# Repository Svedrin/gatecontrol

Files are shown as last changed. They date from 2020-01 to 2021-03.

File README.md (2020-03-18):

# GateControl

ESP8266 firmware that implements a garage gate controller.

# Physical setup

You'll need:

* a garage gate equipped with a motor
* one sensor each at the top and bottom end positions to locate the gate
* a light barrier
* WiFi, MQTT
* a signal light with which you warn people before automatically closing the gate.

# NodeRED

For GUI and for controlling the signal light, I use NodeRED. Here's the flow:

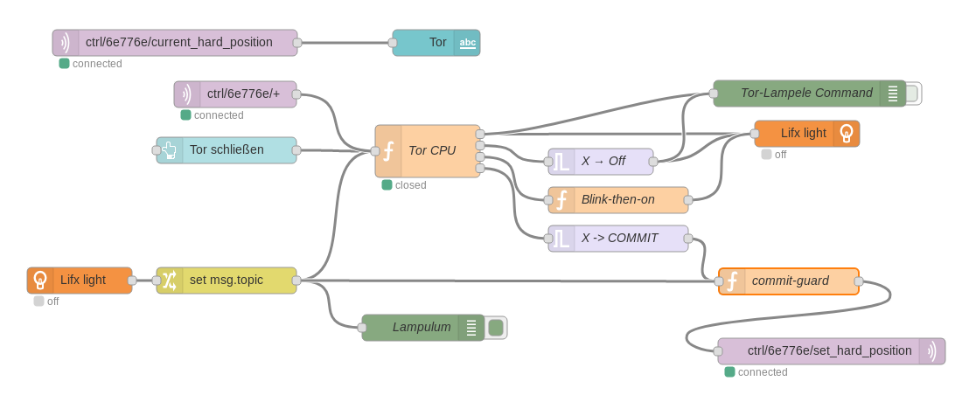
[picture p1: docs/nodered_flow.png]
nodered_flow


The main part of the setup is [the CPU node](nodered/cpu.js). Its state machine can be admired here:

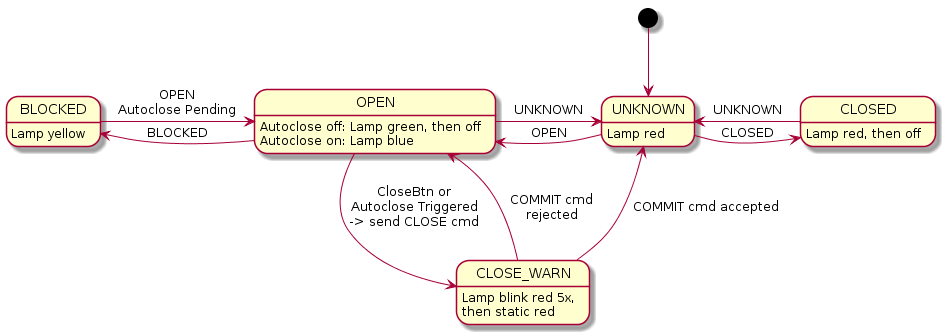
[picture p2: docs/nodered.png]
nodered


# Status indication

The controller regularly publishes the current state of the gate on the `ctrl/<ChipID>/current_hard_position` MQTT topic. You can (and should) use this information to drive a signal light, or monitor for the `ERROR` state.

I'm using a LIFX light bulb for the signal light:

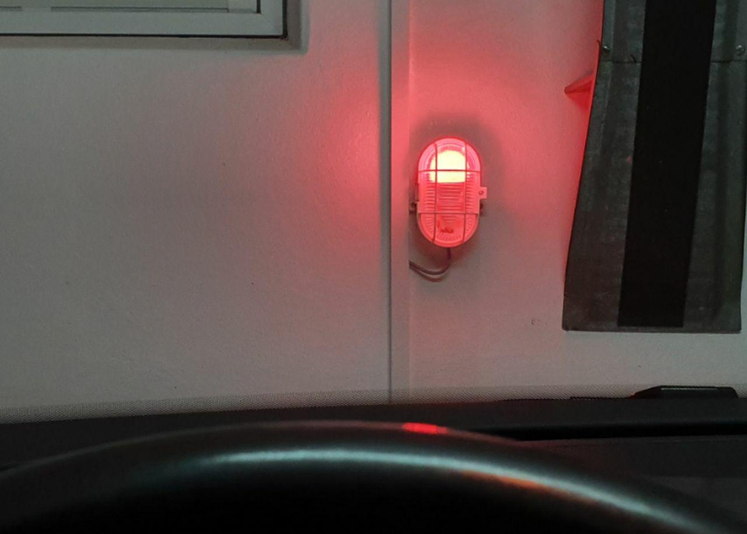
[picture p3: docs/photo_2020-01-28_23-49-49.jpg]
signal


# Controller State Machine

The controller's state machine is focused on providing all the features in a safe way. That means, whatever weird situation we're faced with, the objective is to never make it _worse_. This is achieved by inserting yield points into the state machine, where external commands are necessary to continue. If such a command arrives, we can safely assume that warnings are taken care of. Otherwise, we cannot know what's going on, so we have to abort and return to a safe state.

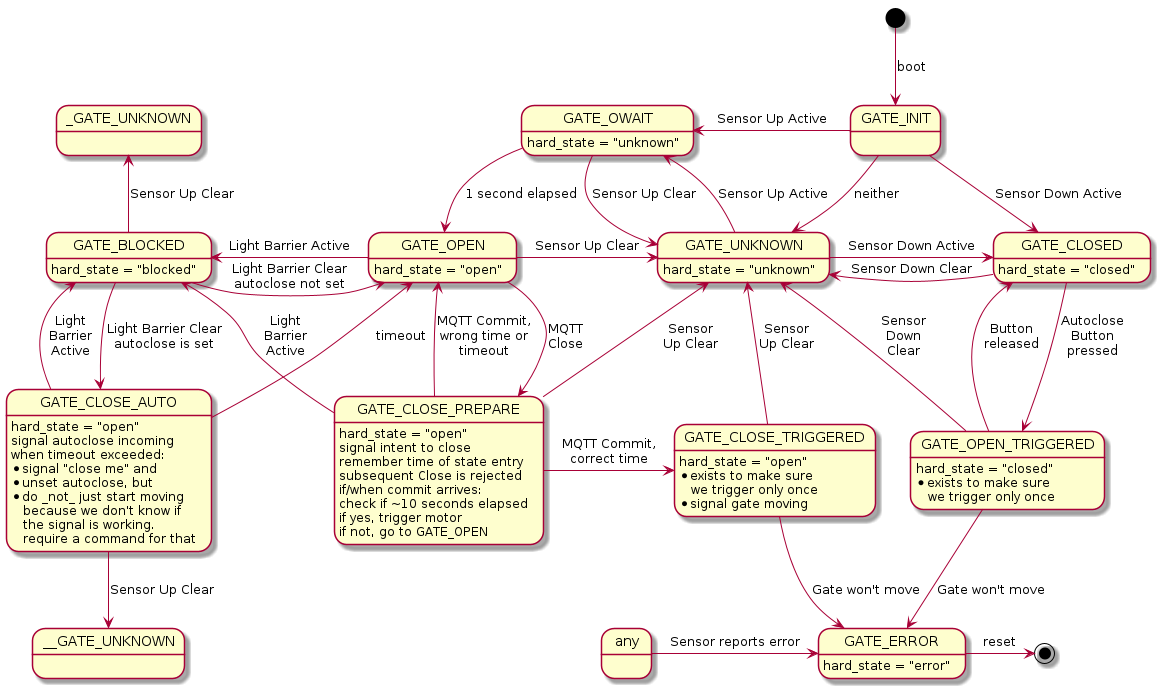
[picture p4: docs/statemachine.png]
statemachine


# Autoclosing

When you want to leave the garage, having to close the gate manually can be a nuisance. Thus the controller supports autoclose, through a separate physical button connected to one of the inputs. The controller then monitors the light barrier, and if it was clear for a while, automatically closes the gate. Again, using the status indications published on `ctrl/<ChipID>/autoclose` to drive a signal light is highly encouraged.

# Remote closing

To command the controller to close the gate:

* send an MQTT message of `CLOSED` to `ctrl/<ChipID>/set_hard_position`.
* If the controller accepted the command, it acknowledges by sending `waiting` to the `ctrl/<ChipID>/close_ack` topic.
* You should now trigger the signal light to show a warning that indicates clearly that the gate is about to move.
* 10 seconds (± some wiggle room) after you sent the initial `CLOSED` command, send `COMMIT` to `ctrl/<ChipID>/set_hard_position`.
* If the controller is satisfied with your timing, it replies with `commit` on `ctrl/<ChipID>/close_ack`.
* The controller triggers the gate to start moving and sends `closing` on `ctrl/<ChipID>/close_ack`.

This scheme basically implements [two-phase commit](https://en.wikipedia.org/wiki/Two-phase_commit_protocol). It is meant to ensure that when individual components fail (like the signal light being unavailable or NodeRED being restarted), the gate does not start moving unexpectedly.

# ESP Pinout

Here's how things need to be connected to the ESP. Comments indicate glitches and caveats, most of which are to do with earlier versions of my PCB being less than ideal. I'll probably need to re-do mine so that I can fix these.

All inputs need to be pulled low when they are active, and high otherwise.

| Input | Pin | Output | Comment |
| --- | --- | --- | --- |
| Sensor Monitor | D0 | | not yet implemented |
| Sensor Up | D1 | | needs external pull-up |
| Sensor Down | D2 | | needs external pull-up |
| Autoclose button | D3 | | must not be pulled low during boot |
| | D4 | Error LED | ESP on-board LED, LOW = on |
| | D5 | Gate Trigger | HIGH = on |
| Lightbarrier blocked | D6 | | |
| Lightbarrier clear | D7 | | |
| | D8 | Status LED | HIGH = on |

Note that while it would probably be better to drive the Status LED and the trigger relay by pulling their pins LOW, we can't really do that since that would incur quirky boot behavior. We really do _not_ want the gate to start moving uncontrollably whenever the ESP is reset, and those pins are pulled LOW during boot, so LOW _must_ mean "off".

Also note that I'm thinking about re-using the Status LED to also drive a relay to enable the Light Barrier only when needed. In that case its behavior would change, because blinking would be a really bad idea (or I'd need to debounce that in the hardware, ugh).

# LEDs

* Error LED: Blinks while connecting to WiFi, off while running, static when error
* Status LED: Static when autoclose enabled, blinks when about to close

# Disclaimer

I broke my gate once during this project, and it's somewhat probable that so will you. I'm obviously not liable for any damages you cause using this project.

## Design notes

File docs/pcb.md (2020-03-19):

# PCB design

The PCB is designed using Fritzing. The breadboard part is not overly accurate and probably won't work (the relays don't fit).

# Relay: SONGLE SRD-05VDC-SL-C

The Fritzing part is from here:

https://github.com/bluewalk/Fritzing-Parts/tree/master/SRD-5VDC-SL-C

Amazon Link for the relays:

https://www.amazon.de/gp/product/B009APPHAE/ref=ppx_yo_dt_b_asin_title_o00_s00?ie=UTF8&psc=1

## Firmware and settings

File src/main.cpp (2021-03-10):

#pragma GCC diagnostic push  // save compiler settings
#pragma GCC diagnostic error "-Wall"

// kate: hl c++
#include <ESP8266WiFi.h>
#include <PubSubClient.h>

// this file #defines WIFI_SSID and WIFI_PASSWORD
#include <WifiParams.h>

#include <monitoredsensor.h>
#include <statemachine.h>

#define PIN_MON        D0 // Low while all sensors are working
#define PIN_UP         D1 // Low when the gate is up
#define PIN_DN         D2 // Low when the gate is down
#define PIN_AUTOCLOSE  D3 // Low when user presses the autoclose button
#define PIN_ERRORLED   D4 // Blinks while connecting, off while running, static when error
#define PIN_TRIGGER    D5 // Relay that triggers the gate
#define PIN_LB_BLOCKED D6 // Light barrier says "I'm blocked"
#define PIN_LB_CLEAR   D7 // Light barrier says "I'm clear"
#define PIN_STATUSLED  D8 // Static when autoclose enabled, blinks when about to close

WiFiClient espClient;
PubSubClient client(espClient);
StateMachine state_machine;
MonitoredSensor light_barrier(PIN_LB_BLOCKED, PIN_LB_CLEAR, LOW, true);

unsigned long last_tick;
unsigned long last_msg;
char hard_pos[50];
char prev_hard_pos[50];

char mqtt_topic_state[50];
char mqtt_topic_commands[50];
char mqtt_topic_command_acks[50];
char mqtt_topic_autoclose[50];

#define MQTT_TOPIC(which_one, topic_suffix) strncpy( \
        which_one, \
        ("ctrl/" + String(ESP.getChipId(), HEX) + "/" + topic_suffix).c_str(), \
        sizeof(which_one) \
    )

void on_mqtt_message(char* topic, byte* payload, unsigned int length);

void reconnect() {
    // Loop until we're reconnected
    while (!client.connected()) {
        Serial.print("Attempting MQTT connection...");
        // Attempt to connect
        String clientId = "ESP8266Client-" + String(ESP.getChipId(), HEX);
        if (client.connect(clientId.c_str(), MQTT_USERNAME, MQTT_PASSWORD)) {
            client.subscribe(mqtt_topic_commands);
            Serial.println("connected");
        } else {
            Serial.print("failed, rc=");
            Serial.print(client.state());
            Serial.println(" try again in 5 seconds");
            // Wait 5 seconds before retrying
            delay(5000);
        }
    }
}

void setup(void)
{
    // Configure pins
    pinMode(PIN_MON,        INPUT);
    pinMode(PIN_UP,         INPUT);
    pinMode(PIN_DN,         INPUT);
    pinMode(PIN_AUTOCLOSE,  INPUT_PULLUP);
    pinMode(PIN_LB_BLOCKED, INPUT_PULLUP);
    pinMode(PIN_LB_CLEAR,   INPUT_PULLUP);

    pinMode(PIN_ERRORLED,  OUTPUT);
    pinMode(PIN_STATUSLED, OUTPUT);
    pinMode(PIN_TRIGGER,   OUTPUT);

    digitalWrite(PIN_ERRORLED,  LOW);
    digitalWrite(PIN_STATUSLED, LOW);
    digitalWrite(PIN_TRIGGER,   LOW);

    // Start Serial
    Serial.begin(115200);

    // Populate topic names
    MQTT_TOPIC(mqtt_topic_state,        "current_hard_position");
    MQTT_TOPIC(mqtt_topic_commands,     "set_hard_position");
    MQTT_TOPIC(mqtt_topic_command_acks, "close_ack");
    MQTT_TOPIC(mqtt_topic_autoclose,    "autoclose");

    Serial.print("State topic: ");
    Serial.println(mqtt_topic_state);

    // Connect to WiFi
    int error_led_state = LOW;
    WiFi.begin(WIFI_SSID, WIFI_PASSWORD);
    WiFi.mode(WIFI_STA);
    Serial.println();
    while (WiFi.status() != WL_CONNECTED) {
        digitalWrite(PIN_ERRORLED, error_led_state);
        error_led_state = (error_led_state == HIGH ? LOW : HIGH);
        delay(500);
        Serial.print(".");
    }
    Serial.println("");
    Serial.println("WiFi connected");
    digitalWrite(PIN_ERRORLED,  HIGH);

    // Print the IP address
    Serial.println(WiFi.localIP());

    randomSeed(micros());

    client.setServer(MQTT_HOST, MQTT_PORT);
    client.setCallback(on_mqtt_message);

    last_tick = 0;
    last_msg  = 0;
}


void on_mqtt_message(char* topic, byte* payload, unsigned int length) {
    char buf[50];
    if( length > sizeof(buf) - 1 ){
        length = sizeof(buf) - 1;
    }
    memcpy(buf, payload, length);
    buf[length] = 0;

    Serial.print("Message arrived [");
    Serial.print(topic);
    Serial.print("] = ");
    Serial.print(buf);

    if( strcmp(topic, mqtt_topic_commands) == 0 ){
        if(strncmp((const char *)payload, "CLOSED", length) == 0){
            Serial.println("Received CLOSE message");
            if (state_machine.cmd_close(millis()) == COMMAND_ACCEPTED) {
                client.publish(mqtt_topic_command_acks, "waiting");
            } else {
                client.publish(mqtt_topic_command_acks, "reject");
            }
        }
        else if(strncmp((const char *)payload, "COMMIT", length) == 0){
            Serial.println("Received COMMIT message");
            if (state_machine.cmd_commit(millis()) == COMMAND_ACCEPTED) {
                client.publish(mqtt_topic_command_acks, "commit");
            } else {
                client.publish(mqtt_topic_command_acks, "abort");
            }
        }
    }
}

void loop() {
    if (!client.connected()) {
        reconnect();
    }

    client.loop();

    unsigned long now = millis();

    if(now > last_tick + 100){
        last_tick = now;

        esp_state_t esp_state;
        esp_state.sensor_gate_up   = (digitalRead(PIN_UP) == LOW ? SENSOR_ACTIVE : SENSOR_CLEAR);
        esp_state.sensor_gate_down = (digitalRead(PIN_DN) == LOW ? SENSOR_ACTIVE : SENSOR_CLEAR);
        esp_state.button_autoclose = (digitalRead(PIN_AUTOCLOSE) == LOW ? SENSOR_ACTIVE : SENSOR_CLEAR);
        esp_state.sensor_light_barrier = light_barrier.read(now);
        esp_state.millis = now;

        step_t step = state_machine.step(&esp_state);

        switch(step.current_state){
            case GATE_INIT:
                strcpy(hard_pos, "INIT");
                break;

            case GATE_OPEN:
            case GATE_CLOSE_AUTO:
            case GATE_CLOSE_PREPARE:
            case GATE_CLOSE_TRIGGERED:
                strcpy(hard_pos, "OPEN");
                break;

            case GATE_BLOCKED:
                strcpy(hard_pos, "BLOCKED");
                break;

            case GATE_OWAIT:
            case GATE_UNKNOWN:
                strcpy(hard_pos, "UNKNOWN");
                break;

            case GATE_CLOSED:
            case GATE_OPEN_TRIGGERED:
                strcpy(hard_pos, "CLOSED");
                break;

            case GATE_ERROR:
                strcpy(hard_pos, "ERROR");
                digitalWrite(PIN_ERRORLED, LOW);
                break;
        }

        if(now > last_msg + 1000 || strcmp(hard_pos, prev_hard_pos) != 0){
            last_msg = now;
            strcpy(prev_hard_pos, hard_pos);
            client.publish(mqtt_topic_state, hard_pos);

            Serial.print("Hard position = ");
            Serial.println(hard_pos);
        }

        // autoclose_state indicates when certain events have happened
        // and are only set for the one step where they happened
        if (step.autoclose_state == AUTOCLOSE_ENABLED) {
            client.publish(mqtt_topic_autoclose, "enabled");
        }
        else if (step.autoclose_state == AUTOCLOSE_PENDING) {
            client.publish(mqtt_topic_autoclose, "pending");
        }
        else if (step.autoclose_state == AUTOCLOSE_RESET) {
            client.publish(mqtt_topic_autoclose, "reset");
        }
        else if (step.autoclose_state == AUTOCLOSE_TRIGGERED) {
            client.publish(mqtt_topic_autoclose, "triggered");
        }

        // Drive the status LED.
        // When we received a CLOSE command, blink (by only lighting
        // up for the second half of each second)
        if (step.current_state == GATE_CLOSE_PREPARE) {
            digitalWrite(PIN_STATUSLED, (now % 1000 > 500 ? HIGH : LOW));
        }
        // When autoclose is enabled, light up statically
        else if (step.autoclose_state == AUTOCLOSE_ON) {
            digitalWrite(PIN_STATUSLED, HIGH);
        }
        // Otherwise, go dark
        else {
            digitalWrite(PIN_STATUSLED, LOW);
        }

        if (step.trigger) {
            Serial.println("trigger! pew pew");
            digitalWrite(PIN_TRIGGER, HIGH);
            delay(500);
            digitalWrite(PIN_TRIGGER, LOW);
        }
    }

    delay(1);
}

#pragma GCC diagnostic pop // Restore compiler settings

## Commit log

2020-01-22 refactor LOW and HIGH to SENSOR_ACTIVE and SENSOR_CLEAR
2020-01-22 install wheel support for setuptools
2020-01-22 missed an edge case
2020-01-23 treat warnings as errors, but only in my own code
    [main.cpp]
2020-01-23 add defines for all the pins, plus docs on what the LEDs mean
2020-01-23 move pin configuration to the top of setup()
2020-01-23 implement error led
2020-01-23 rename led_state to error_led_state for clarification
    [main.cpp]
2020-01-23 drive the status LED
2020-01-23 add note about the light barrier relay
2020-01-23 catch SENSOR_ERROR on the autoclose button
2020-01-25 add test for when gate starts moving before the button is released
2020-01-25 test_autoclose_from_open is not an edge case; rename others for clarity
2020-01-25 both up and down sensor being active is an error condition
2020-01-25 add support for relay-type sensors where monitor and active cannot be enabled at the same tme
2020-01-27 add screenshot of the nodered flow
2020-01-28 add test for (and fix bug in) when autoclose has triggered and is then interrupted
2020-01-28 send AUTOCLOSE_RESET when the user intervenes and pushes buttons
2020-03-18 add Fritzing diagram [WIP]
    [pcb.fzz]
2020-03-19 replace the relay with one we can actually order, finish the PCB
    [pcb.fzz]
2020-03-19 got rid of one of the relays
    [pcb.fzz]
2020-06-19 manually routed by da Pr0z
    [pcb.fzz]
2021-03-10 add GATE_OWAIT state, fix test_init_open IT [WIP]
    [main.cpp]
